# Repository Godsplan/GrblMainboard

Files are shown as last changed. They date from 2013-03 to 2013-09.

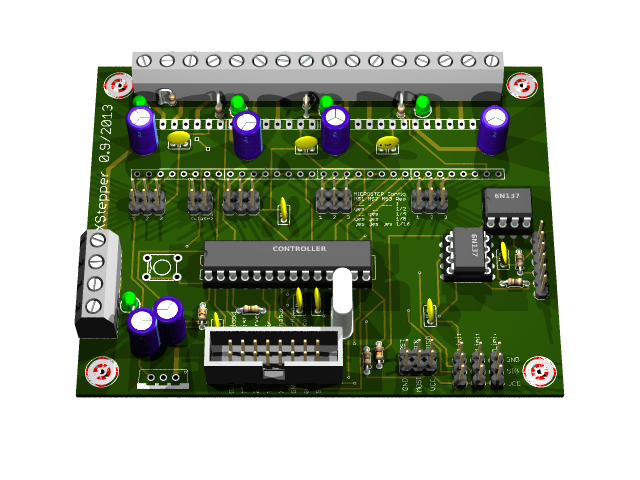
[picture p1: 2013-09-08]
eagle3d/XStepper.bmp

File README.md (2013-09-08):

GrblMainboard - v3.0
=============

A new Solution with Grbl Firmware to use cnc mills or 3d printers.

created by Christoph Kielhorn (Godsplan), Frank Herrmann (xpix)

---------------

The GrblMainboard includes the following features:

- ATMega328u (DIL Package)
- USB Connection using USB-FTDI
- Opto-Couplers for USB Connection
- ICSP-Connector for flashing the firmware
- GRBL Firmware (v0.8) and GRBL Pinout
- Connector for External Buttons for spindle, reset, etc...
- Support for four Pololu A4988 or Pololu DRV8825 Modules
- Supports dual-Y motion
- Supports cooling fan
- Supports XYZ-Limit in extra pinheader
- LED's for every axis
- LED's for every Limit
- Power LED
- AK500 Screw terminal for Steppers
- Connector for Bluetooth TTL Modules

---------------
v3.3	- GrblMainboard Backfork
- Added Pin Locations
- Added I2C Connectors for Sensors

v0.9.1 - XStepper Development

- add optional pullup resistors (1k/5V) for Hallo Sesnor switches (Cherry MP101401)
   http://www.cherrycorp.com/english/sensors/pdf/MP1014_Series.pdf

v0.9 - Initial Development

- created schema files
- created .brd

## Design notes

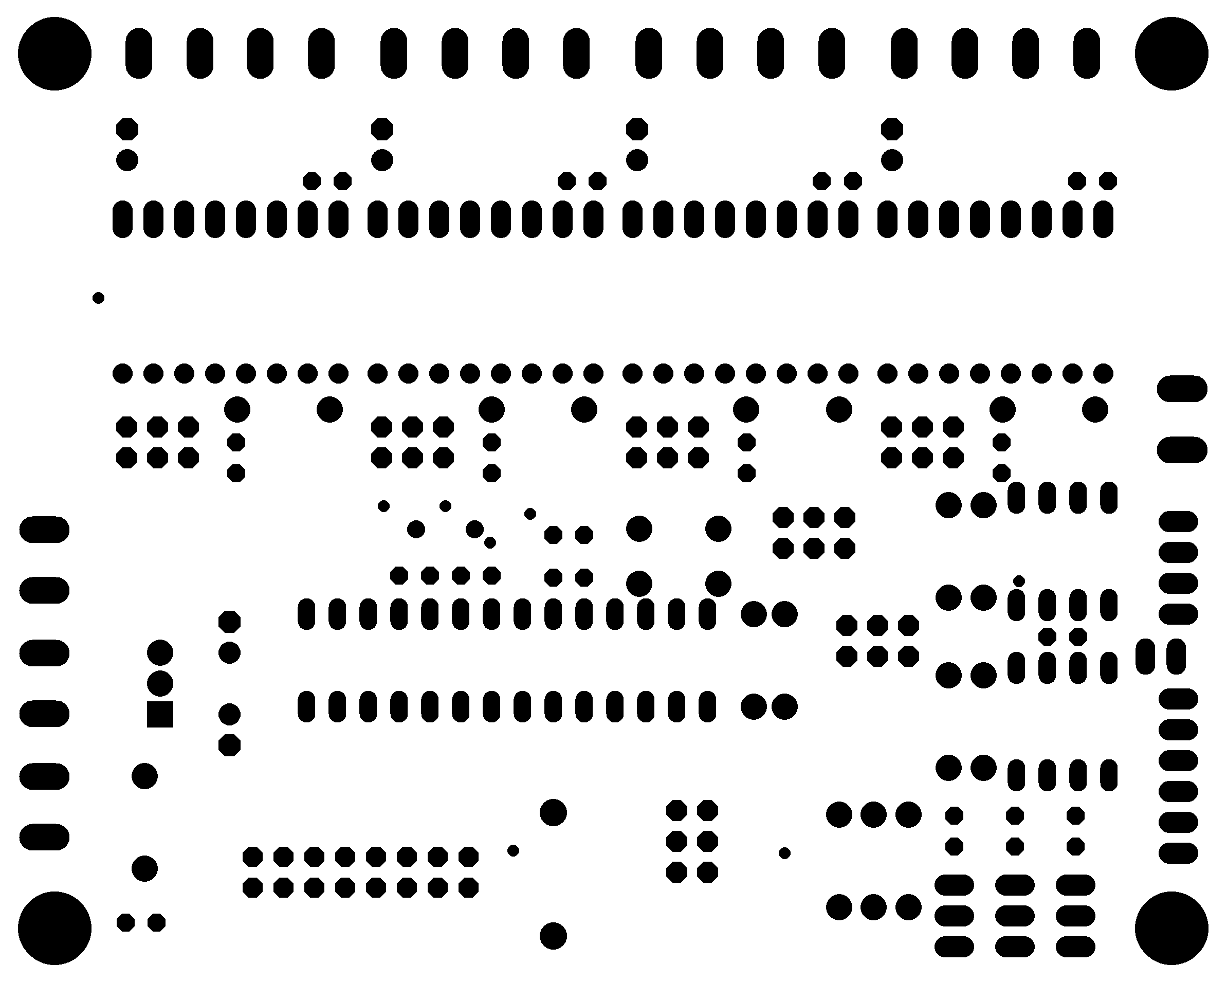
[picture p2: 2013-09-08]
eagleUp/eagleUp_XStepper_bottom_mask.png

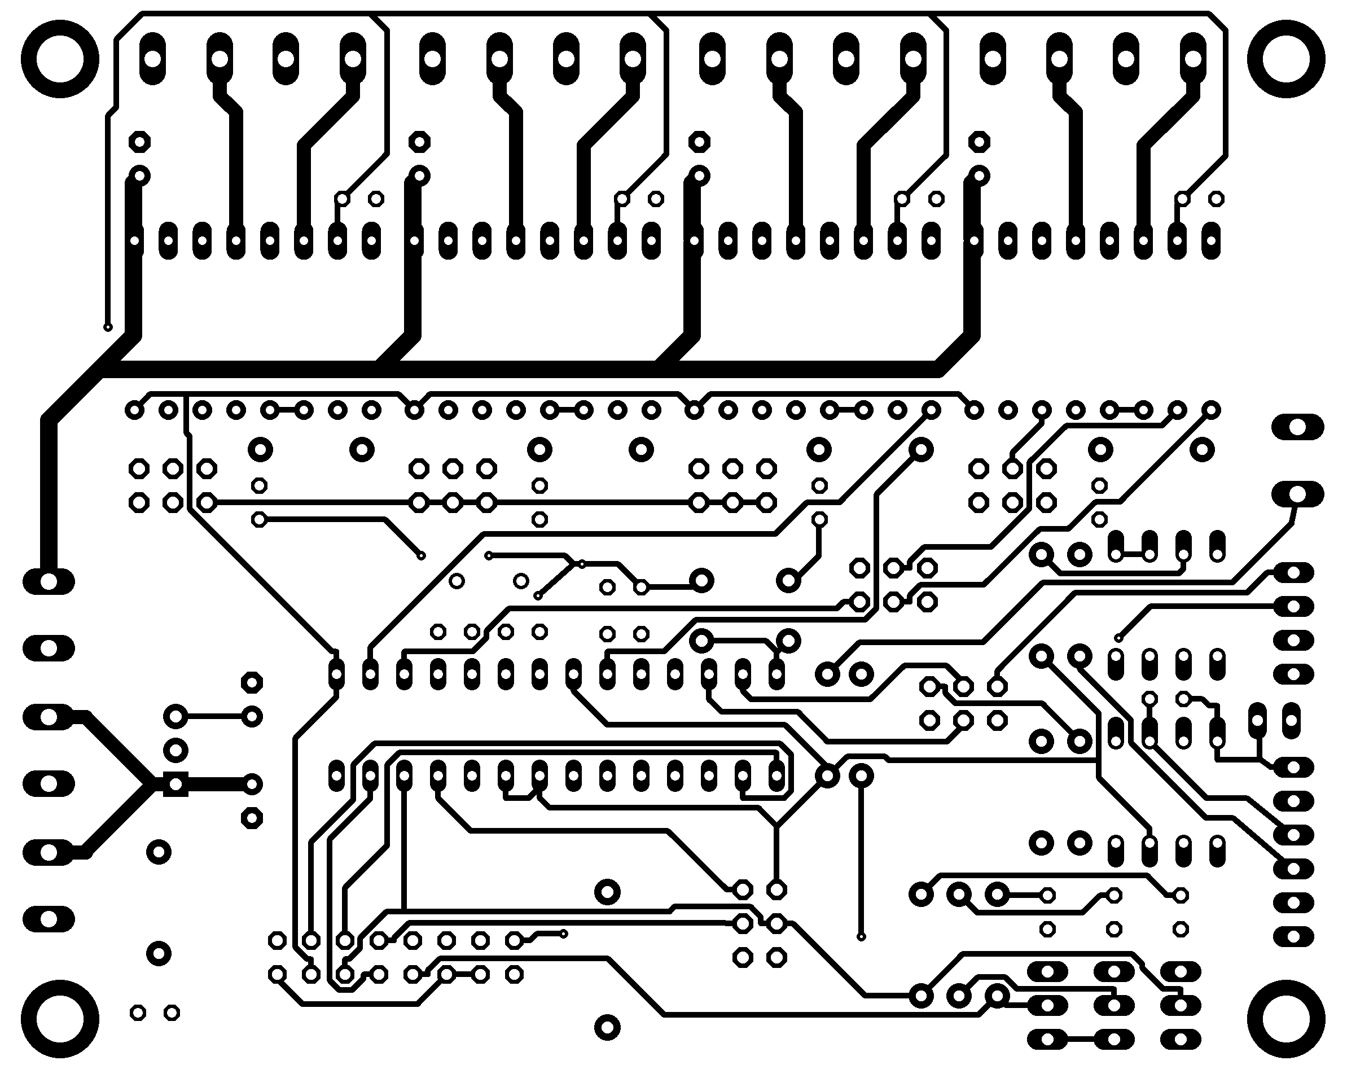
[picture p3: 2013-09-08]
eagleUp/eagleUp_XStepper_top.png

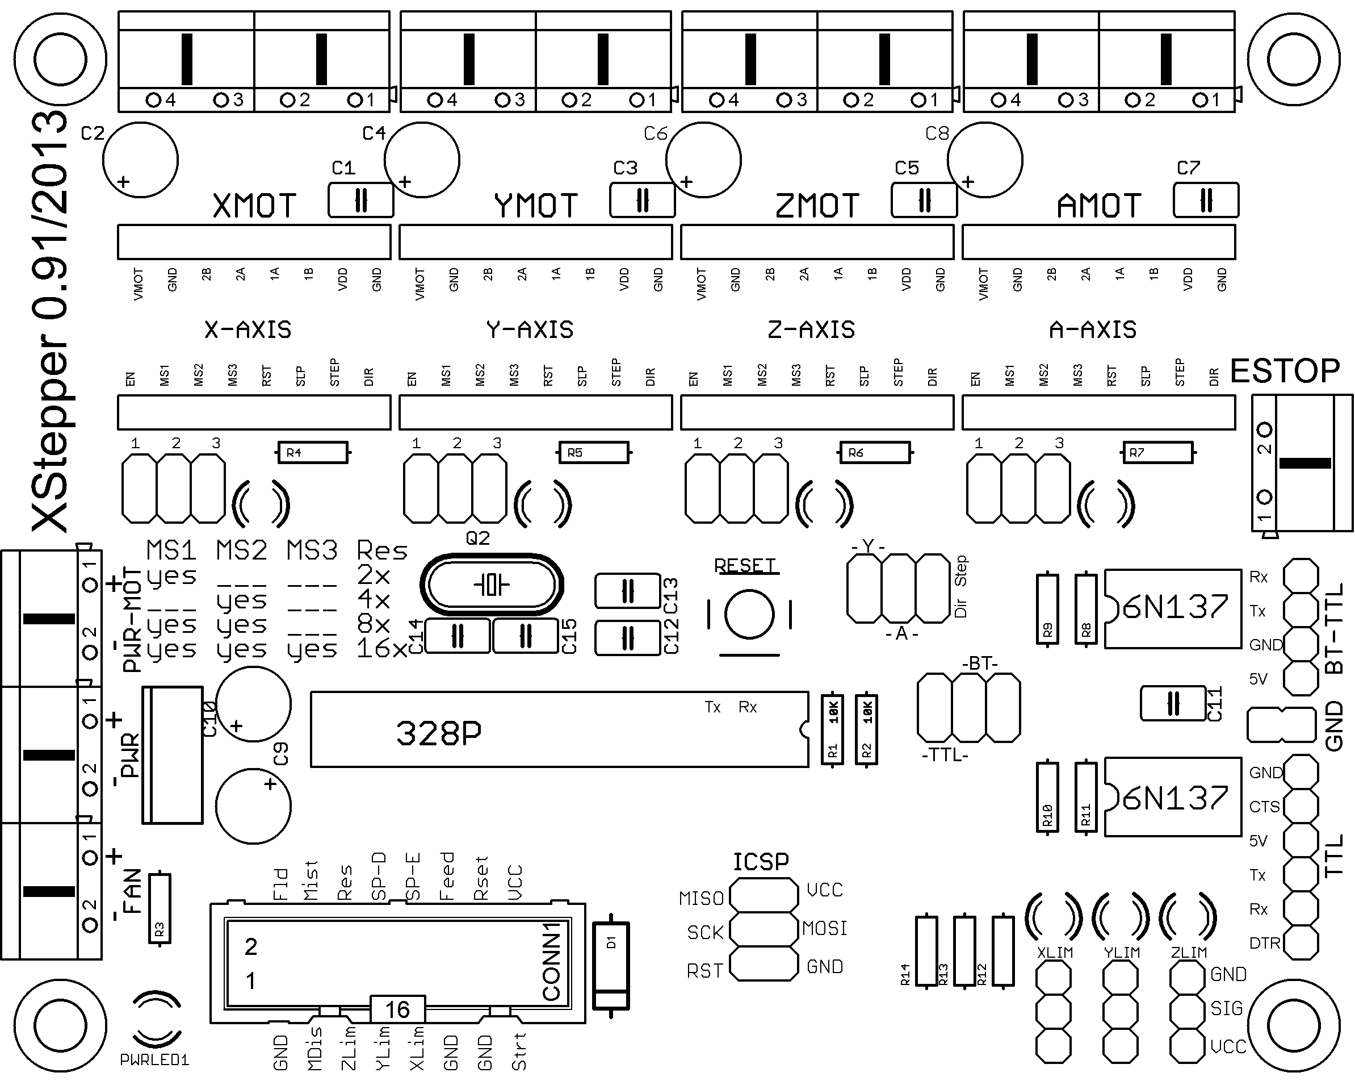
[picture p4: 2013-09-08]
eagleUp/eagleUp_XStepper_top_silk.png

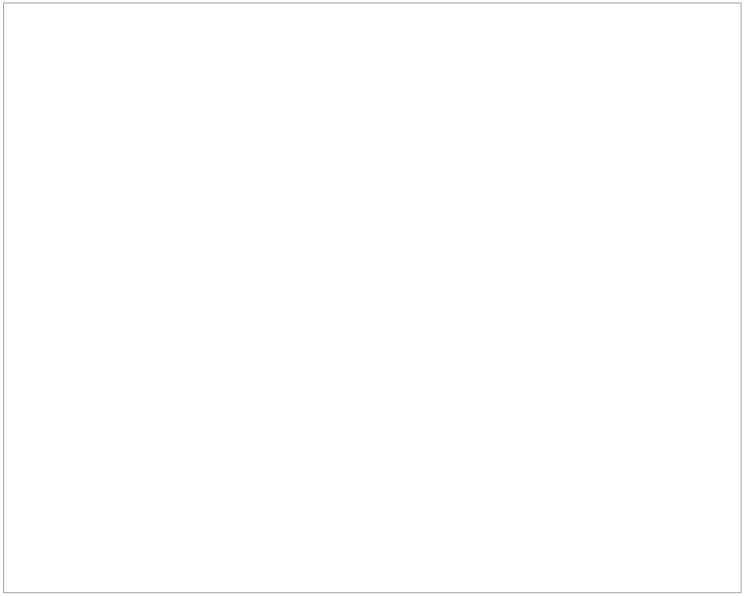
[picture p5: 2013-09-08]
eagleUp/eagleUp_XStepper_outline.png

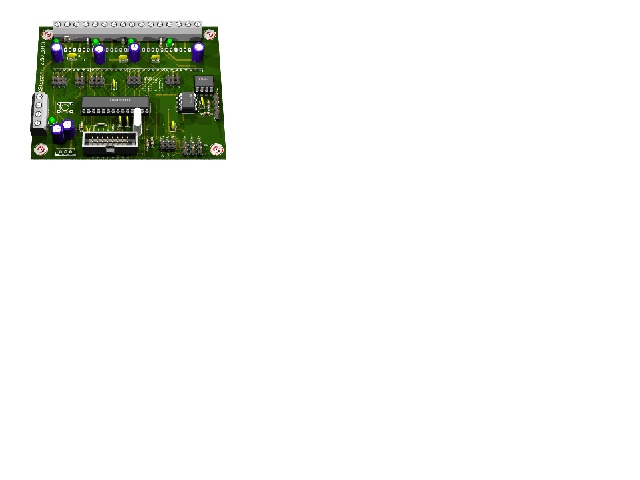
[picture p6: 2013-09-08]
eagle3d/XStepper_mini.jpg

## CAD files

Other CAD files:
eagleUp/XStepper.skp

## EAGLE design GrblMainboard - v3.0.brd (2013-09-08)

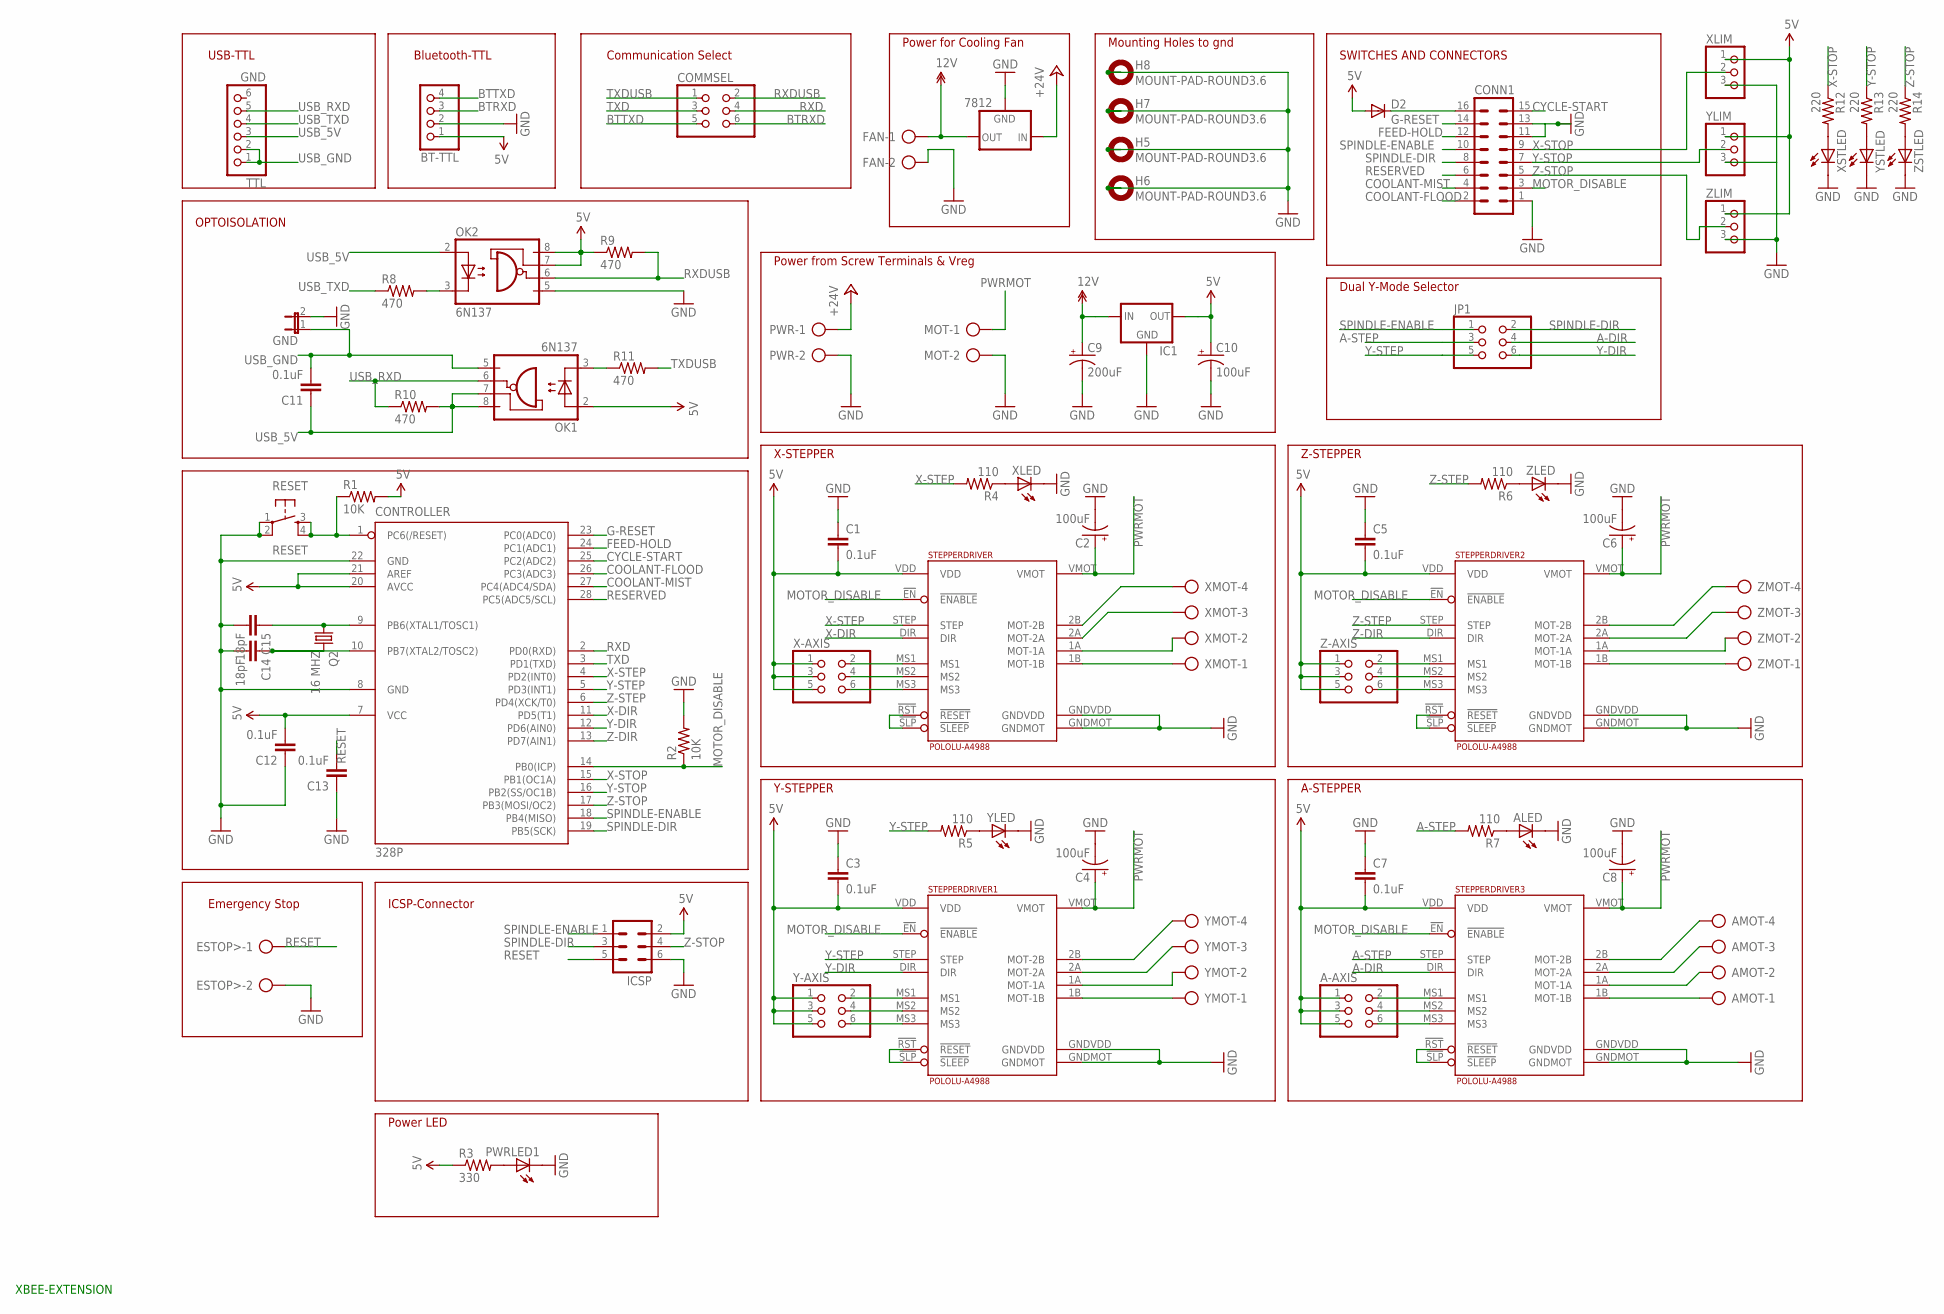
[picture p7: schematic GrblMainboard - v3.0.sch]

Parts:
328P: CONTROLLER; DIL28-3
7812: V_REG_78XXSINK; TO220-IGO
A-AXIS: PINHD-2X3; 2X03
ALED: LED3MM
AMOT: AK500/4
BT-TTL: PINHD-1X4; 1X04
C1, C3, C5, C7, C11, C12, C13: 0.1uF; C025-025X050
C2, C4, C6, C8: 100uF; E3,5-8
C9: 200uF; E2,5-6
C10: 100uF; E2,5-6
C14, C15: 18pF; C025-025X050
COMMSEL: PINHD-2X3; 2X03
CONN1: ML16
D2: DIODEPTH; DIODE-1N4001
ESTOP>: AK500/2
FAN: AK500/2
GND: JP1E; JP1
H5, H6, H7, H8: MOUNT-PAD-ROUND3.6; 3,6-PAD
IC1: V_REG_78XXSINK; TO220-IGO
ICSP: ML6
JP1: PINHD-2X3; 2X03
MOT: AK500/2
OK1, OK2: 6N137; DIL08
PWR: AK500/2
PWRLED1: LED3MM
Q2: 16 MHZ; HC49/S
R1, R2: 10K; AXIAL-0.3
R3: 330; 1/6W-RES
R4, R5, R6, R7: 110; AXIAL-0.3
R8, R9, R10, R11: 470; AXIAL-0.3
R12, R13, R14: 220; AXIAL-0.3
RESET: RESET; TACTILE-PTH
STEPPERDRIVER, STEPPERDRIVER1, STEPPERDRIVER2, STEPPERDRIVER3: POLOLU-A4988; POLOLU-ALLEGRO-PTH
TTL: GND; 1X06
X-AXIS: PINHD-2X3; 2X03
XLED: LED3MM
XLIM: PINHD-1X3; 1X03
XMOT: AK500/4
XSTLED: LED3MM
Y-AXIS: PINHD-2X3; 2X03
YLED: LED3MM
YLIM: PINHD-1X3; 1X03
YMOT: AK500/4
YSTLED: LED3MM
Z-AXIS: PINHD-2X3; 2X03
ZLED: LED3MM
ZLIM: PINHD-1X3; 1X03
ZMOT: AK500/4
ZSTLED: LED3MM

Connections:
5V: 328P.7 (VCC), 328P.20 (AVCC), 328P.21 (AREF), A-AXIS.1, A-AXIS.3, A-AXIS.5, BT-TTL.1, C1.2, C3.2, C5.2, C7.2, C10.+, C12.2, D2.A, IC1.OUT, ICSP.2, OK1.2 (A), OK2.7 (VE), OK2.8 (VCC), R1.P$2 (2), R3.1, R9.P$1 (1), STEPPERDRIVER.VDD, STEPPERDRIVER1.VDD, STEPPERDRIVER2.VDD, STEPPERDRIVER3.VDD, X-AXIS.1, X-AXIS.3, X-AXIS.5, XLIM.1, Y-AXIS.1, Y-AXIS.3, Y-AXIS.5, YLIM.1, Z-AXIS.1, Z-AXIS.3, Z-AXIS.5, ZLIM.1
12V: 7812.OUT, C9.+, FAN.1, IC1.IN
+24V: 7812.IN, PWR.1
A-DIR: JP1.4, STEPPERDRIVER3.DIR
A-STEP: JP1.3, R7.P$2 (2), STEPPERDRIVER3.STEP
BTRXD: BT-TTL.3, COMMSEL.6
BTTXD: BT-TTL.4, COMMSEL.5
COOLANT-FLOOD: 328P.26 (PC3(ADC3)), CONN1.2
COOLANT-MIST: 328P.27 (PC4(ADC4/SDA)), CONN1.4
CYCLE-START: 328P.25 (PC2(ADC2)), CONN1.15
FEED-HOLD: 328P.24 (PC1(ADC1)), CONN1.12
G-RESET: 328P.23 (PC0(ADC0)), CONN1.14
GND: 328P.8 (GND), 328P.22 (GND), 7812.GND, ALED.K (C), BT-TTL.2, C1.1, C2.-, C3.1, C4.-, C5.1, C6.-, C7.1, C8.-, C9.-, C10.-, C12.1, C13.1, C14.2, C15.2, CONN1.1, CONN1.11, CONN1.13, ESTOP>.2, FAN.2, GND.2, H5.B3,6, H6.B3,6, H7.B3,6, H8.B3,6, IC1.GND, ICSP.6, MOT.2, OK2.5 (GND), PWR.2, PWRLED1.K (C), R2.P$2 (2), RESET.1, RESET.2, STEPPERDRIVER.GNDMOT, STEPPERDRIVER.GNDVDD, STEPPERDRIVER1.GNDMOT, STEPPERDRIVER1.GNDVDD, STEPPERDRIVER2.GNDMOT, STEPPERDRIVER2.GNDVDD, STEPPERDRIVER3.GNDMOT, STEPPERDRIVER3.GNDVDD, XLED.K (C), XLIM.3, XSTLED.K (C), YLED.K (C), YLIM.3, YSTLED.K (C), ZLED.K (C), ZLIM.3, ZSTLED.K (C)
MOTOR_DISABLE: 328P.14 (PB0(ICP)), CONN1.3, R2.P$1 (1), STEPPERDRIVER.!EN (!ENABLE), STEPPERDRIVER1.!EN (!ENABLE), STEPPERDRIVER2.!EN (!ENABLE), STEPPERDRIVER3.!EN (!ENABLE)
unnamed: STEPPERDRIVER.1B (MOT-1B), XMOT.1
unnamed: STEPPERDRIVER.1A (MOT-1A), XMOT.2
unnamed: STEPPERDRIVER.2A (MOT-2A), XMOT.3
unnamed: STEPPERDRIVER.2B (MOT-2B), XMOT.4
unnamed: STEPPERDRIVER.!RST (!RESET), STEPPERDRIVER.!SLP (!SLEEP)
unnamed: STEPPERDRIVER.MS1, X-AXIS.2
unnamed: STEPPERDRIVER.MS2, X-AXIS.4
unnamed: STEPPERDRIVER.MS3, X-AXIS.6
unnamed: STEPPERDRIVER1.1B (MOT-1B), YMOT.1
unnamed: STEPPERDRIVER1.1A (MOT-1A), YMOT.2
unnamed: STEPPERDRIVER1.2A (MOT-2A), YMOT.3
unnamed: STEPPERDRIVER1.2B (MOT-2B), YMOT.4
unnamed: STEPPERDRIVER1.!RST (!RESET), STEPPERDRIVER1.!SLP (!SLEEP)
unnamed: STEPPERDRIVER1.MS1, Y-AXIS.2
unnamed: STEPPERDRIVER1.MS2, Y-AXIS.4
unnamed: STEPPERDRIVER1.MS3, Y-AXIS.6
unnamed: STEPPERDRIVER2.2B (MOT-2B), ZMOT.4
unnamed: STEPPERDRIVER2.2A (MOT-2A), ZMOT.3
unnamed: STEPPERDRIVER2.1A (MOT-1A), ZMOT.2
unnamed: STEPPERDRIVER2.1B (MOT-1B), ZMOT.1
unnamed: STEPPERDRIVER2.!RST (!RESET), STEPPERDRIVER2.!SLP (!SLEEP)
unnamed: STEPPERDRIVER2.MS1, Z-AXIS.2
unnamed: STEPPERDRIVER2.MS2, Z-AXIS.4
unnamed: STEPPERDRIVER2.MS3, Z-AXIS.6
unnamed: AMOT.1, STEPPERDRIVER3.1B (MOT-1B)
unnamed: AMOT.2, STEPPERDRIVER3.1A (MOT-1A)
unnamed: AMOT.3, STEPPERDRIVER3.2A (MOT-2A)
unnamed: AMOT.4, STEPPERDRIVER3.2B (MOT-2B)
unnamed: STEPPERDRIVER3.!RST (!RESET), STEPPERDRIVER3.!SLP (!SLEEP)
unnamed: A-AXIS.2, STEPPERDRIVER3.MS1
unnamed: A-AXIS.4, STEPPERDRIVER3.MS2
unnamed: A-AXIS.6, STEPPERDRIVER3.MS3
unnamed: 328P.9 (PB6(XTAL1/TOSC1)), C15.1, Q2.1
unnamed: 328P.10 (PB7(XTAL2/TOSC2)), C14.1, Q2.2
unnamed: OK2.3 (C), R8.P$2 (2)
unnamed: OK1.3 (C), R11.P$1 (1)
unnamed: R12.P$2 (2), XSTLED.A
unnamed: R4.P$1 (1), XLED.A
unnamed: R5.P$1 (1), YLED.A
unnamed: R6.P$1 (1), ZLED.A
unnamed: ALED.A, R7.P$1 (1)
unnamed: R13.P$2 (2), YSTLED.A
unnamed: PWRLED1.A, R3.2
unnamed: R14.P$2 (2), ZSTLED.A
unnamed: CONN1.16, D2.C
PWRMOT: C2.+, C4.+, C6.+, C8.+, MOT.1, STEPPERDRIVER.VMOT, STEPPERDRIVER1.VMOT, STEPPERDRIVER2.VMOT, STEPPERDRIVER3.VMOT
RESERVED: 328P.28 (PC5(ADC5/SCL)), CONN1.6
RESET: 328P.1 (PC6(/RESET)), C13.2, ESTOP>.1, ICSP.5, R1.P$1 (1), RESET.3, RESET.4
RXD: 328P.2 (PD0(RXD)), COMMSEL.4
RXDUSB: COMMSEL.2, OK2.6 (VO), R9.P$2 (2)
SPINDLE-DIR: 328P.19 (PB5(SCK)), CONN1.8, ICSP.3, JP1.2
SPINDLE-ENABLE: 328P.18 (PB4(MISO)), CONN1.10, ICSP.1, JP1.1
TXD: 328P.3 (PD1(TXD)), COMMSEL.3
TXDUSB: COMMSEL.1, R11.P$2 (2)
USB_5V: C11.1, OK1.7 (VE), OK1.8 (VCC), OK2.2 (A), R10.P$2 (2), TTL.3
USB_GND: C11.2, GND.1, OK1.5 (GND), TTL.1, TTL.2
USB_RXD: OK1.6 (VO), R10.P$1 (1), TTL.5
USB_TXD: R8.P$1 (1), TTL.4
X-DIR: 328P.11 (PD5(T1)), STEPPERDRIVER.DIR
X-STEP: 328P.4 (PD2(INT0)), R4.P$2 (2), STEPPERDRIVER.STEP
X-STOP: 328P.15 (PB1(OC1A)), CONN1.9, R12.P$1 (1), XLIM.2
Y-DIR: 328P.12 (PD6(AIN0)), JP1.6, STEPPERDRIVER1.DIR
Y-STEP: 328P.5 (PD3(INT1)), JP1.5, R5.P$2 (2), STEPPERDRIVER1.STEP
Y-STOP: 328P.16 (PB2(SS/OC1B)), CONN1.7, R13.P$1 (1), YLIM.2
Z-DIR: 328P.13 (PD7(AIN1)), STEPPERDRIVER2.DIR
Z-STEP: 328P.6 (PD4(XCK/T0)), R6.P$2 (2), STEPPERDRIVER2.STEP
Z-STOP: 328P.17 (PB3(MOSI/OC2)), CONN1.5, ICSP.4, R14.P$1 (1), ZLIM.2

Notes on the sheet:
X-STEPPER
Y-STEPPER
Z-STEPPER
Power from Screw Terminals & Vreg
A-STEPPER
Dual Y-Mode Selector
OPTOISOLATION
Power for Cooling Fan
ICSP-Connector
Mounting Holes to gnd
XBEE-EXTENSION
USB-TTL
SWITCHES AND CONNECTORS
Power LED
Bluetooth-TTL
Emergency Stop
Communication Select

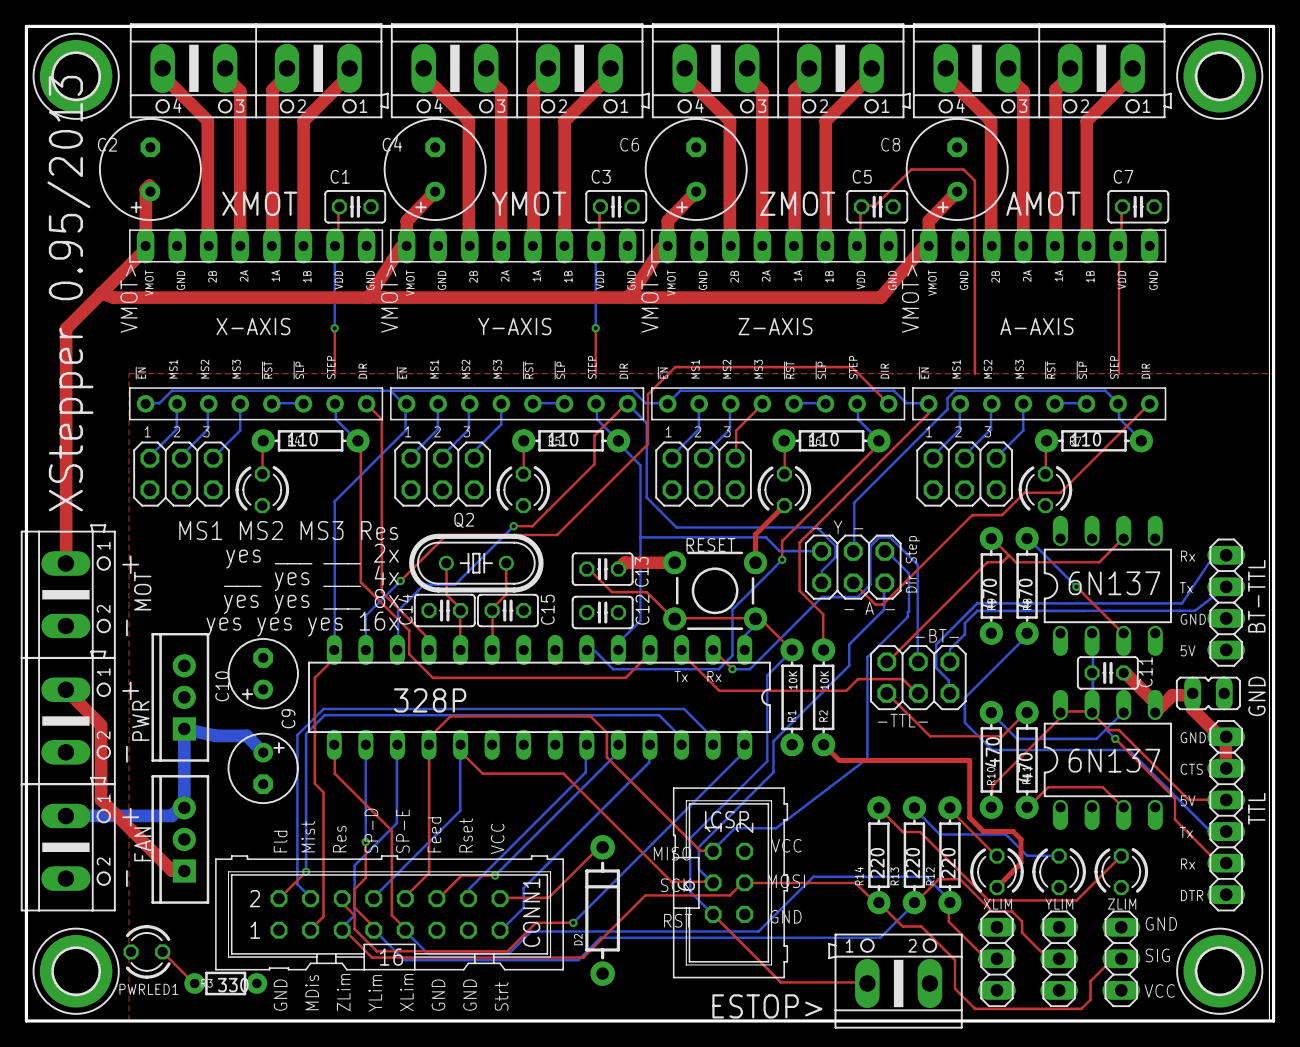
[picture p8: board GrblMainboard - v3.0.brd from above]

Board: 2 copper layers, 100.3 x 80.0 mm, 75 parts (0 on the bottom side), 81 nets.

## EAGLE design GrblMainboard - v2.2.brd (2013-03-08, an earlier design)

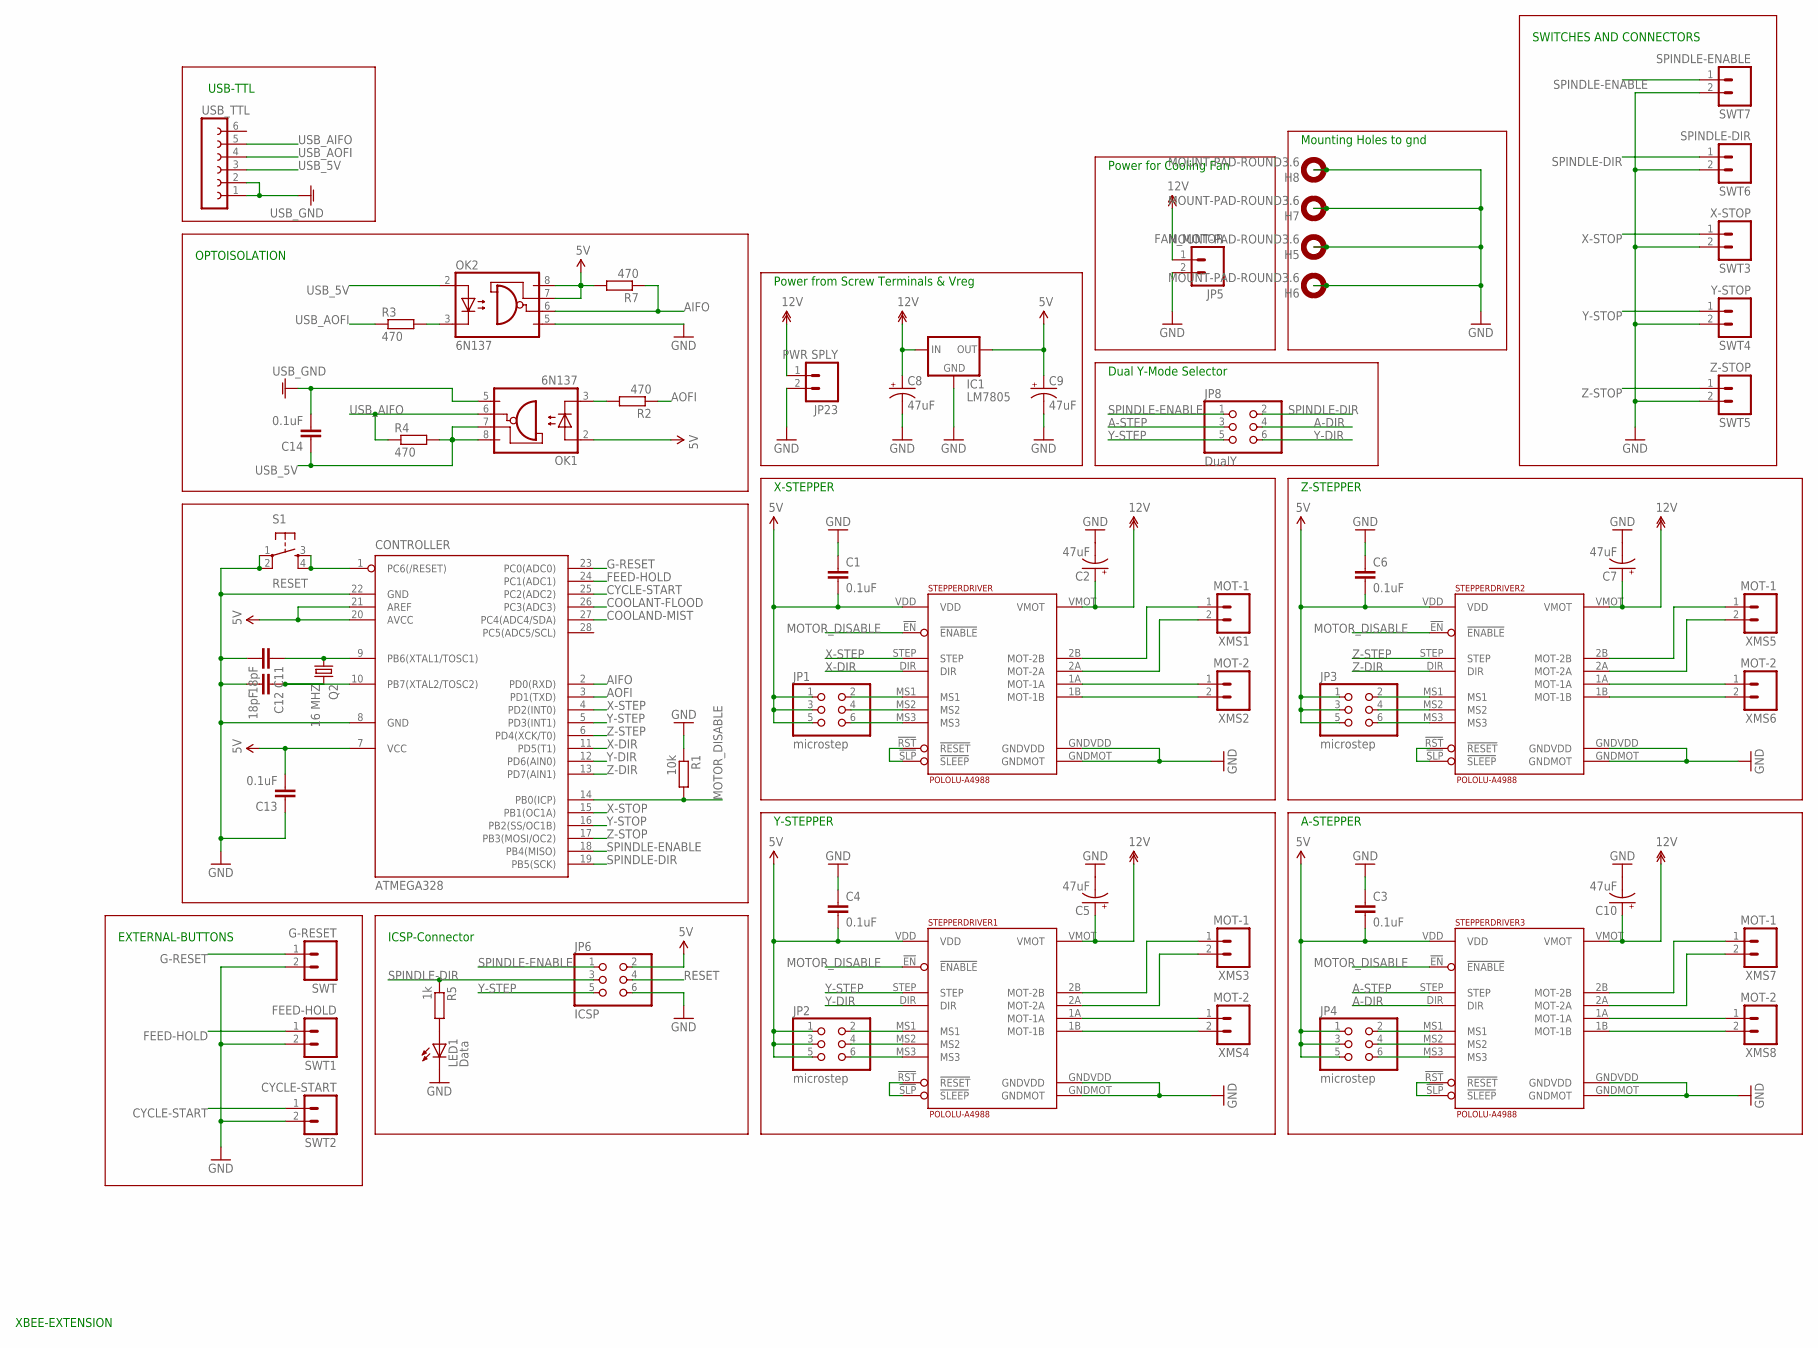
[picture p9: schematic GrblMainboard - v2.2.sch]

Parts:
ATMEGA328: CONTROLLER; DIL28-3
C1, C3, C4, C6: 0.1uF; C025-025X050
C2, C5, C7, C8, C9, C10: 47uF; E2,5-6
C11, C12: 18pF; CAP-PTH-SMALL2
C13, C14: 0.1uF; CAP-PTH-SMALL2
H5, H6, H7, H8: MOUNT-PAD-ROUND3.6; 3,6-PAD
IC1: LM7805; 78XXL-CUSTOM
JP1, JP2, JP3, JP4: microstep; 2X03
JP5: FAN_MOTOR; SCREWTERMINAL-5MM-2
JP6: ICSP; 2X03
JP8: DualY; 2X03
JP23: PWR SPLY; SCREWTERMINAL-5MM-2
LED1: Data; LED5MM
OK1, OK2: 6N137; DIL08
Q2: 16 MHZ; HC49/S
R1: 10k; 0207/10
R2, R3, R4, R7: 470; 0207/12
R5: 1k; 0207/10
S1: RESET; TACTILE-PTH
STEPPERDRIVER, STEPPERDRIVER1, STEPPERDRIVER2, STEPPERDRIVER3: POLOLU-A4988; POLOLU-ALLEGRO-PTH
SWT: G-RESET; SCREWTERMINAL-5MM-2
SWT1: FEED-HOLD; SCREWTERMINAL-5MM-2
SWT2: CYCLE-START; SCREWTERMINAL-5MM-2
SWT3: X-STOP; SCREWTERMINAL-5MM-2
SWT4: Y-STOP; SCREWTERMINAL-5MM-2
SWT5: Z-STOP; SCREWTERMINAL-5MM-2
SWT6: SPINDLE-DIR; SCREWTERMINAL-5MM-2
SWT7: SPINDLE-ENABLE; SCREWTERMINAL-5MM-2
USB_TTL: FE06-1; FE06
XMS1, XMS3, XMS5, XMS7: MOT-1; SCREWTERMINAL-5MM-2
XMS2, XMS4, XMS6, XMS8: MOT-2; SCREWTERMINAL-5MM-2

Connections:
5V: ATMEGA328.7 (VCC), ATMEGA328.20 (AVCC), ATMEGA328.21 (AREF), C1.2, C3.2, C4.2, C6.2, C9.+, C13.2, IC1.OUT, JP1.1, JP1.3, JP1.5, JP2.1, JP2.3, JP2.5, JP3.1, JP3.3, JP3.5, JP4.1, JP4.3, JP4.5, JP6.2, OK1.2 (A), OK2.7 (VE), OK2.8 (VCC), R7.2, STEPPERDRIVER.VDD, STEPPERDRIVER1.VDD, STEPPERDRIVER2.VDD, STEPPERDRIVER3.VDD
12V: C2.+, C5.+, C7.+, C8.+, C10.+, IC1.IN, JP5.1, JP23.1, STEPPERDRIVER.VMOT, STEPPERDRIVER1.VMOT, STEPPERDRIVER2.VMOT, STEPPERDRIVER3.VMOT
A-DIR: JP8.4, STEPPERDRIVER3.DIR
A-STEP: JP8.3, STEPPERDRIVER3.STEP
AIFO: ATMEGA328.2 (PD0(RXD)), OK2.6 (VO), R7.1
AOFI: ATMEGA328.3 (PD1(TXD)), R2.1
COOLAND-MIST: ATMEGA328.27 (PC4(ADC4/SDA))
COOLANT-FLOOD: ATMEGA328.26 (PC3(ADC3))
CYCLE-START: ATMEGA328.25 (PC2(ADC2)), SWT2.1
FEED-HOLD: ATMEGA328.24 (PC1(ADC1)), SWT1.1
G-RESET: ATMEGA328.23 (PC0(ADC0)), SWT.1
GND: ATMEGA328.8 (GND), ATMEGA328.22 (GND), C1.1, C2.-, C3.1, C4.1, C5.-, C6.1, C7.-, C8.-, C9.-, C10.-, C11.2, C12.2, C13.1, H5.B3,6, H6.B3,6, H7.B3,6, H8.B3,6, IC1.GND, JP5.2, JP6.6, JP23.2, LED1.K (C), OK2.5 (GND), R1.1, S1.1, S1.2, STEPPERDRIVER.GNDMOT, STEPPERDRIVER.GNDVDD, STEPPERDRIVER1.GNDMOT, STEPPERDRIVER1.GNDVDD, STEPPERDRIVER2.GNDMOT, STEPPERDRIVER2.GNDVDD, STEPPERDRIVER3.GNDMOT, STEPPERDRIVER3.GNDVDD, SWT.2, SWT1.2, SWT2.2, SWT3.2, SWT4.2, SWT5.2, SWT6.2, SWT7.2
GNDA: C14.2, OK1.5 (GND), USB_TTL.1, USB_TTL.2
MOTOR_DISABLE: ATMEGA328.14 (PB0(ICP)), R1.2, STEPPERDRIVER.!EN (!ENABLE), STEPPERDRIVER1.!EN (!ENABLE), STEPPERDRIVER2.!EN (!ENABLE), STEPPERDRIVER3.!EN (!ENABLE)
unnamed: STEPPERDRIVER.2B (MOT-2B), XMS1.1
unnamed: STEPPERDRIVER.2A (MOT-2A), XMS1.2
unnamed: STEPPERDRIVER.1A (MOT-1A), XMS2.1
unnamed: STEPPERDRIVER.1B (MOT-1B), XMS2.2
unnamed: STEPPERDRIVER.!RST (!RESET), STEPPERDRIVER.!SLP (!SLEEP)
unnamed: JP1.2, STEPPERDRIVER.MS1
unnamed: JP1.4, STEPPERDRIVER.MS2
unnamed: JP1.6, STEPPERDRIVER.MS3
unnamed: STEPPERDRIVER1.2B (MOT-2B), XMS3.1
unnamed: STEPPERDRIVER1.2A (MOT-2A), XMS3.2
unnamed: STEPPERDRIVER1.1A (MOT-1A), XMS4.1
unnamed: STEPPERDRIVER1.1B (MOT-1B), XMS4.2
unnamed: STEPPERDRIVER1.!RST (!RESET), STEPPERDRIVER1.!SLP (!SLEEP)
unnamed: JP2.2, STEPPERDRIVER1.MS1
unnamed: JP2.4, STEPPERDRIVER1.MS2
unnamed: JP2.6, STEPPERDRIVER1.MS3
unnamed: STEPPERDRIVER2.2B (MOT-2B), XMS5.1
unnamed: STEPPERDRIVER2.2A (MOT-2A), XMS5.2
unnamed: STEPPERDRIVER2.1A (MOT-1A), XMS6.1
unnamed: STEPPERDRIVER2.1B (MOT-1B), XMS6.2
unnamed: STEPPERDRIVER2.!RST (!RESET), STEPPERDRIVER2.!SLP (!SLEEP)
unnamed: JP3.2, STEPPERDRIVER2.MS1
unnamed: JP3.4, STEPPERDRIVER2.MS2
unnamed: JP3.6, STEPPERDRIVER2.MS3
unnamed: STEPPERDRIVER3.2B (MOT-2B), XMS7.1
unnamed: STEPPERDRIVER3.2A (MOT-2A), XMS7.2
unnamed: STEPPERDRIVER3.1A (MOT-1A), XMS8.1
unnamed: STEPPERDRIVER3.1B (MOT-1B), XMS8.2
unnamed: STEPPERDRIVER3.!RST (!RESET), STEPPERDRIVER3.!SLP (!SLEEP)
unnamed: JP4.2, STEPPERDRIVER3.MS1
unnamed: JP4.4, STEPPERDRIVER3.MS2
unnamed: JP4.6, STEPPERDRIVER3.MS3
unnamed: ATMEGA328.9 (PB6(XTAL1/TOSC1)), C11.1, Q2.1
unnamed: ATMEGA328.10 (PB7(XTAL2/TOSC2)), C12.1, Q2.2
unnamed: OK2.3 (C), R3.2
unnamed: OK1.3 (C), R2.2
unnamed: LED1.A, R5.2
RESET: ATMEGA328.1 (PC6(/RESET)), JP6.4, S1.3, S1.4
SPINDLE-DIR: ATMEGA328.19 (PB5(SCK)), JP6.3, JP8.2, R5.1, SWT6.1
SPINDLE-ENABLE: ATMEGA328.18 (PB4(MISO)), JP6.1, JP8.1, SWT7.1
USB_5V: C14.1, OK1.7 (VE), OK1.8 (VCC), OK2.2 (A), R4.2, USB_TTL.3
USB_AIFO: OK1.6 (VO), R4.1, USB_TTL.5
USB_AOFI: R3.1, USB_TTL.4
X-DIR: ATMEGA328.11 (PD5(T1)), STEPPERDRIVER.DIR
X-STEP: ATMEGA328.4 (PD2(INT0)), STEPPERDRIVER.STEP
X-STOP: ATMEGA328.15 (PB1(OC1A)), SWT3.1
Y-DIR: ATMEGA328.12 (PD6(AIN0)), JP8.6, STEPPERDRIVER1.DIR
Y-STEP: ATMEGA328.5 (PD3(INT1)), JP6.5, JP8.5, STEPPERDRIVER1.STEP
Y-STOP: ATMEGA328.16 (PB2(SS/OC1B)), SWT4.1
Z-DIR: ATMEGA328.13 (PD7(AIN1)), STEPPERDRIVER2.DIR
Z-STEP: ATMEGA328.6 (PD4(XCK/T0)), STEPPERDRIVER2.STEP
Z-STOP: ATMEGA328.17 (PB3(MOSI/OC2)), SWT5.1

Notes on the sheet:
X-STEPPER
Y-STEPPER
Z-STEPPER
Power from Screw Terminals & Vreg
A-STEPPER
Dual Y-Mode Selector
OPTOISOLATION
Power for Cooling Fan
ICSP-Connector
Mounting Holes to gnd
XBEE-EXTENSION
EXTERNAL-BUTTONS
USB-TTL
SWITCHES AND CONNECTORS

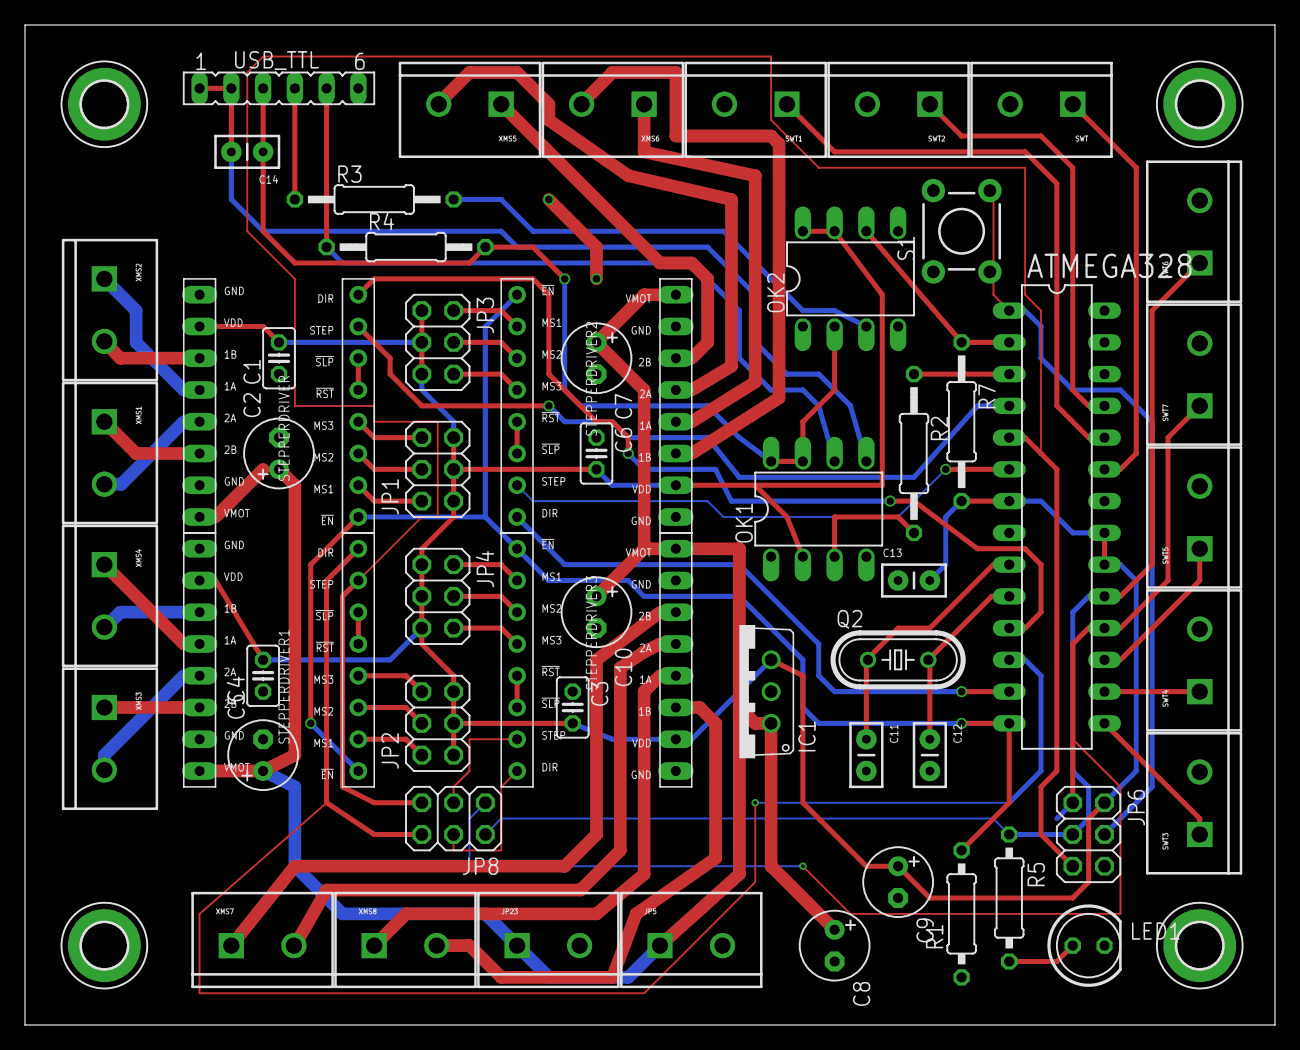
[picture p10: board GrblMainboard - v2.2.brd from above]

Board: 2 copper layers, 100.0 x 80.0 mm, 60 parts (0 on the bottom side), 64 nets.

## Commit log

2013-03-07 Power wires thicker for ~ 3A
    - make power wires thicker
    - check for error in DRU schema and board
    - replace Atmega328U with Atmega328
    [GrblMainboard - v2.1.brd, GrblMainboard - v2.1.sch]
2013-03-08 added mounting holes for CPU Fan
    i added 4 holes to add a 12V CPU Fan
    [GrblMainboard - v2.1.brd, GrblMainboard - v2.1.sch, GrblMainboard - v2.2.brd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]
2013-09-08 Backfork from XStepper
    [XStepper.GBL, XStepper.GBO, XStepper.GBP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]
2013-09-08 cleaning and moving
    [GrblMainboard - v2.2.brd, GrblMainboard - v2.2.sch, GrblMainboard - v3.0.brd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]

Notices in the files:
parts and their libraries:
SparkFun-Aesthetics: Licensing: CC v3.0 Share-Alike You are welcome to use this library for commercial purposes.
